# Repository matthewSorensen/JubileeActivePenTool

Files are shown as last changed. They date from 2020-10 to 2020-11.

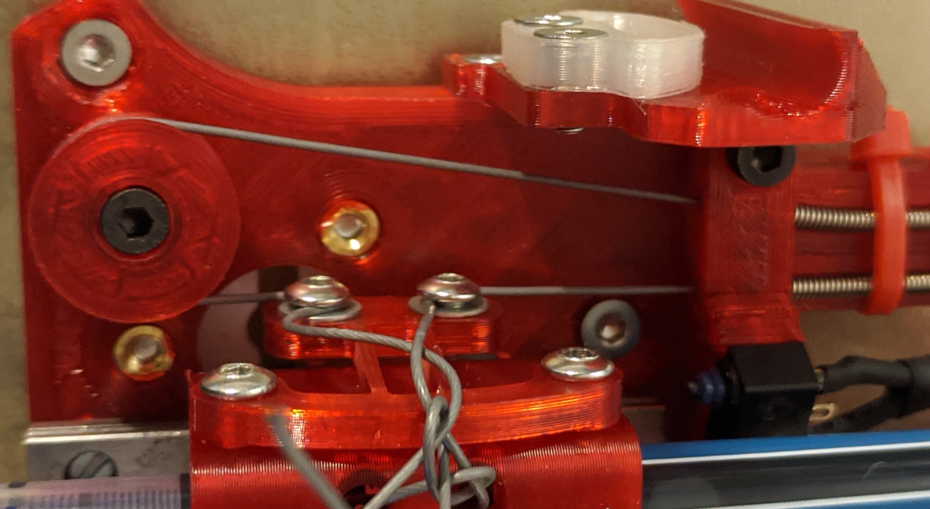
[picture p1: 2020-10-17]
photos/ToolCableRouting.jpg

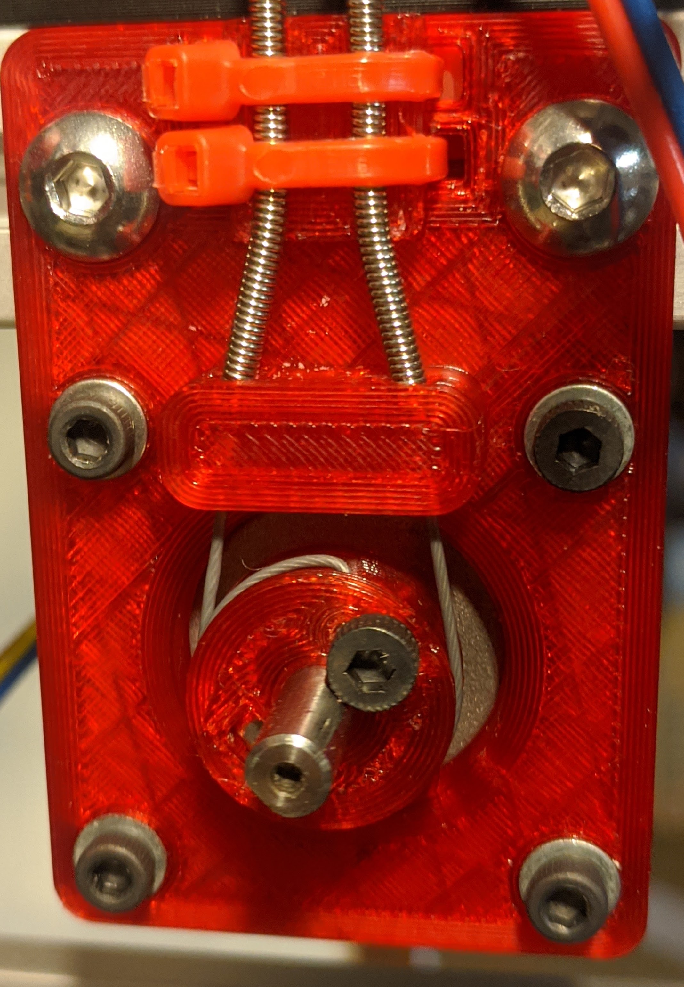
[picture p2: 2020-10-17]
photos/MotorPulley.jpg

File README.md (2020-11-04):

Jubilee Plotter Tool
======

An actively-driven pen plotter toolhead for the [Jubilee](https://jubilee3d.com/) project.

## Limitations!

My machine's "ooze control assembly" is placed significantly lower than on a standard Jubilee, so I have
enough room to mount the motor/pulley assembly on the top bar, directly under the tool dock. In that
configuration, a stock 600mm spring guide is comfortably long enough to cover the full build area. However,
on a stock machine that requires the motor/pulley assembly to be mounted on the lower extrusion, a
longer (650mm?) spring guide is probably a good idea.

At the moment, I'm using a silly large stepper motor - this design is probably compatible with
a smaller "pancake" style stepper, but that is untested at the moment.

## Printed Parts

Print one of each stl in the *meshes* folder in PLA using the [standard Jubilee settings](https://jubilee3d.com/index.php?title=3D_Printed_Parts)
and the provided orientation. Or not, you're a responsible adult and can choose part orientation and
printer settings.

## BOM

* 1x stock Jubilee 600mm spring guide kit, consisting of:

    * 1600mm length of Low-Stretch Coated Wire Rope Braided, 18-8 Stainless Steel, 7 x 19, 0.024" Diameter

    * 2x600mm lengths of SG-088-020-120 spring guide, 0.020" dia wire, 0.088" OD, Type 302 Stainless

* 55mm LWL7B miniature linear rail and carriage

* NEMA17 stepper motor

* 4x M3 brass heated insert nut, McMaster 94180A331 - same used for the rest of the Jubilee build.

* M3 square nut - same used for the rest of the Jubilee build

* 5x M3 Buttonhead Screw, 6mm long (Bolt Depot 7218)

* 5x M3 Buttonhead Screw, 8mm long (Bolt Depot 7219)

* 5x M3 Buttonhead Screw, 12mm long (Bolt Depot 7221)

* 6x M3 washers (Bolt Depot 4513)

* 2x M5 Buttonhead Screw, 10mm long (Bolt Depot 6632)

* 2x M5 drop-in nuts for 20x20 extrusion

* M3 setscrew, 5mm long (Bolt Depot 8706)

* 4x M2.5 screws or bolts, 8mm-10mm long - must have heads compatible with linear rail

* 4x M2 machine screw, 8mm long (Bolt Depot)

* 1x MR103-ZZ bearing (or any 3mm ID/10mm OD/4mm tall bearing)

* 1x standard Jubilee limit switch

* Two strand wire for limit switch

* Small zipties

* 1 set of standard Jubilee tool plate hardware - steel balls, insert nuts, screws, delrin wedge plate etc...

* 4x M3x8 flathead screws (Bolt Depot 7213)

* 4x 5x9x2 Buna-N O-rings (McMaster 9262K165)

## Instructions

Nope, not yet. Ask me on discord - maybe I'll take more photos of the pulley wire routing?

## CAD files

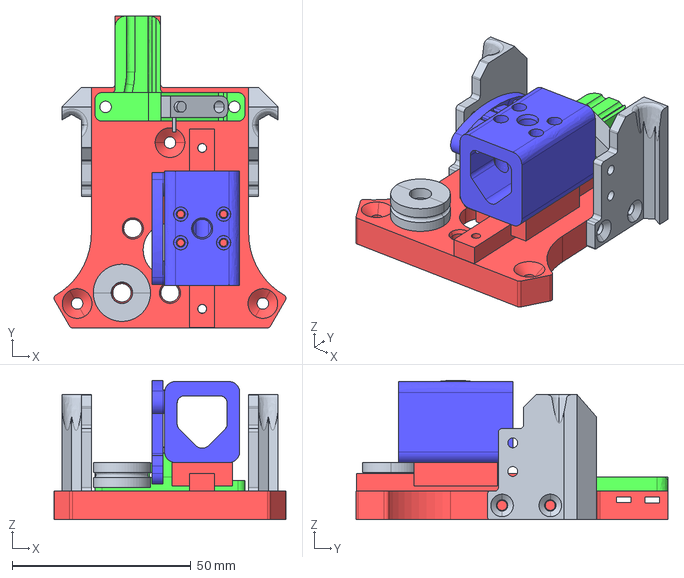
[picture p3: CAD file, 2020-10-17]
meshes/ToolAssembly.stp
64.9 x 87.2 x 39.0 mm

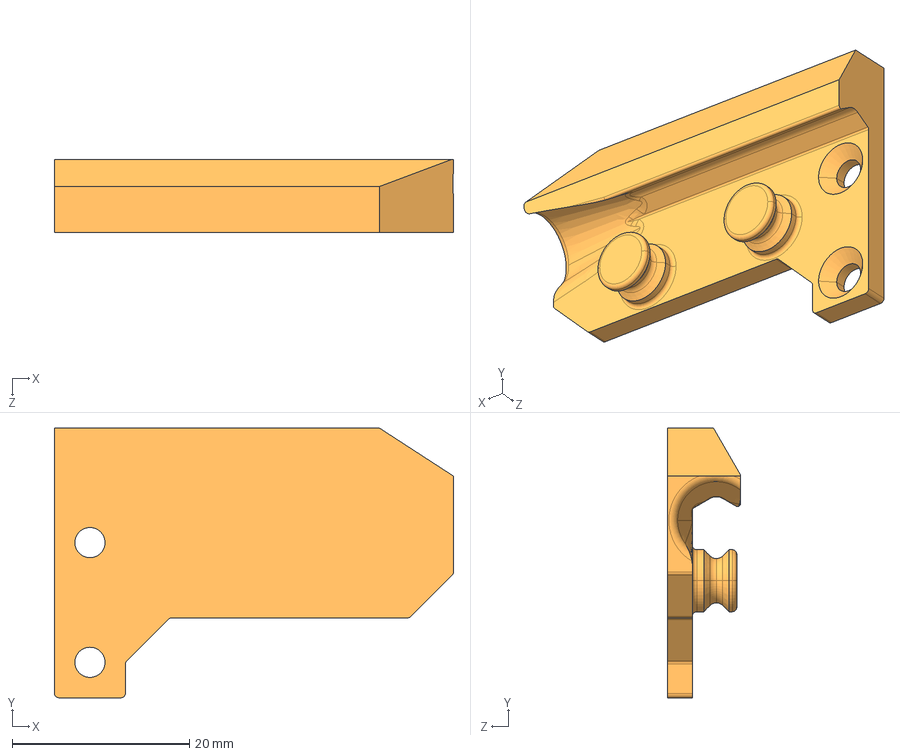
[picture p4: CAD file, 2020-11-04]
meshes/HalfWing.stp
45.0 x 30.4 x 8.20 mm

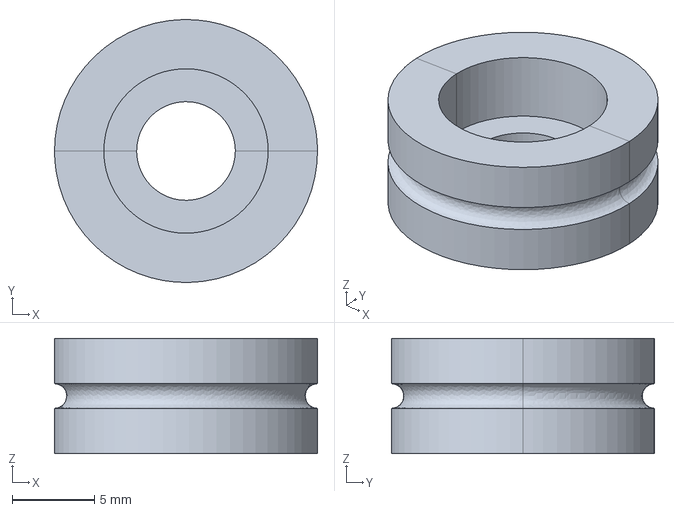
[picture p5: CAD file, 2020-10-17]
meshes/PassivePulley.stp
16.0 x 16.0 x 7.00 mm

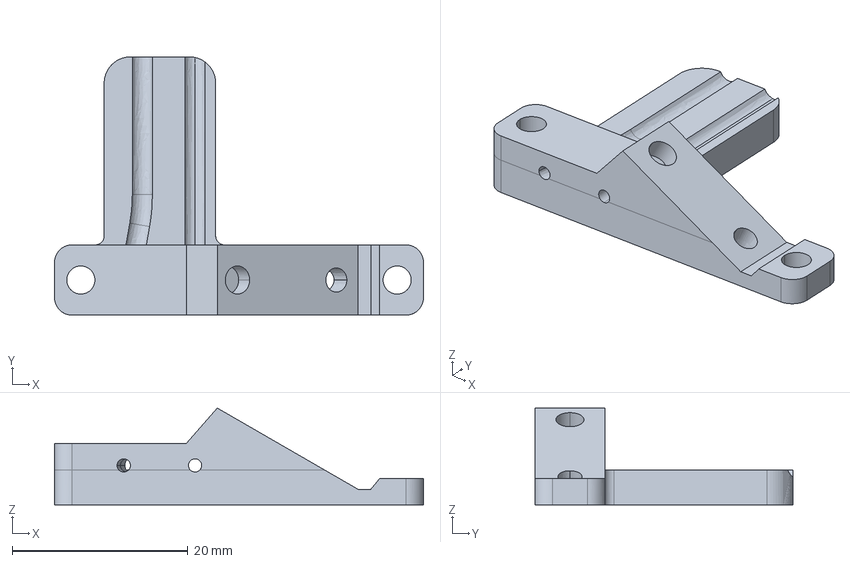
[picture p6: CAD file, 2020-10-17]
meshes/CableHolder.stp
42.0 x 29.4 x 11.0 mm

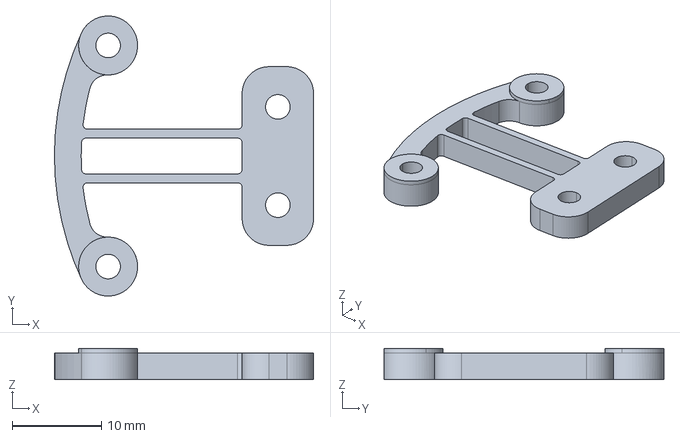
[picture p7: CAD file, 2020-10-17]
meshes/Flexure.stp
29.0 x 31.3 x 3.50 mm

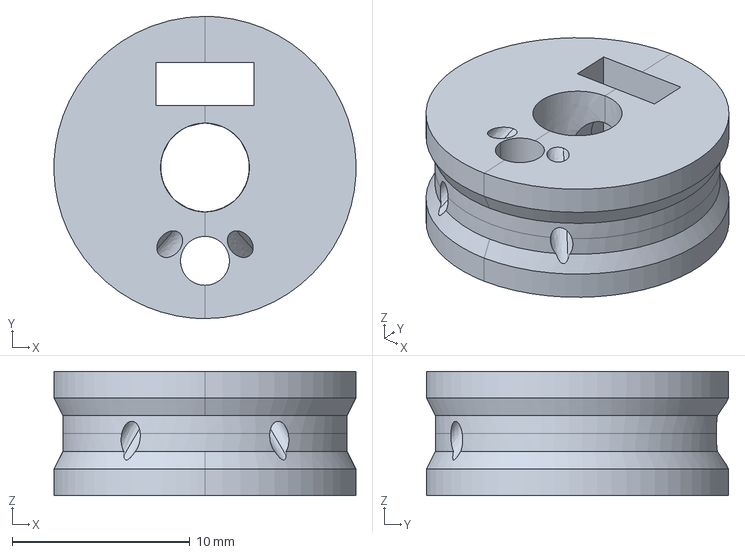
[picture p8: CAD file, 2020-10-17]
meshes/MotorPulley.stp
17.0 x 17.0 x 7.00 mm

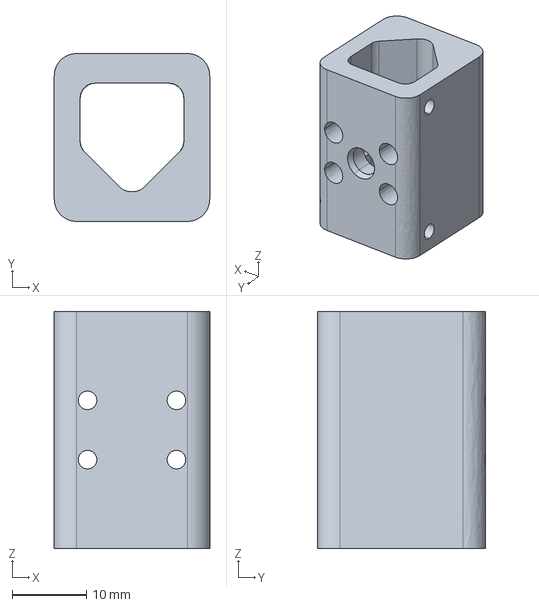
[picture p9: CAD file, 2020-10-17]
meshes/PenHolder.stp
21.0 x 22.7 x 32.0 mm

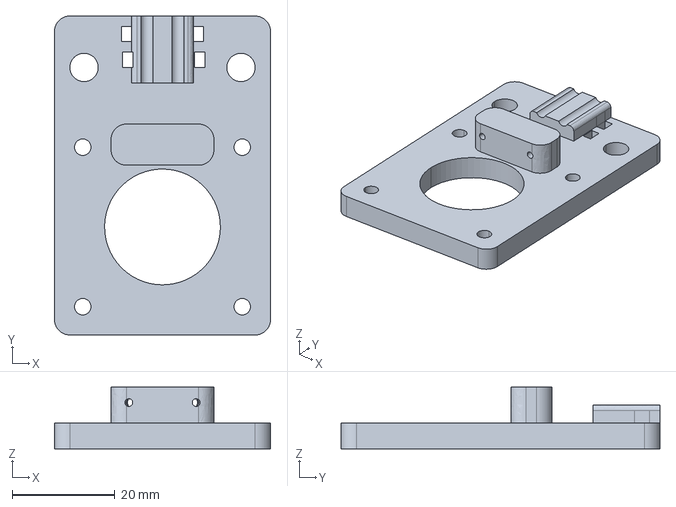
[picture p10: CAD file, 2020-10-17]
meshes/MotorMount.stp
42.0 x 62.0 x 12.0 mm

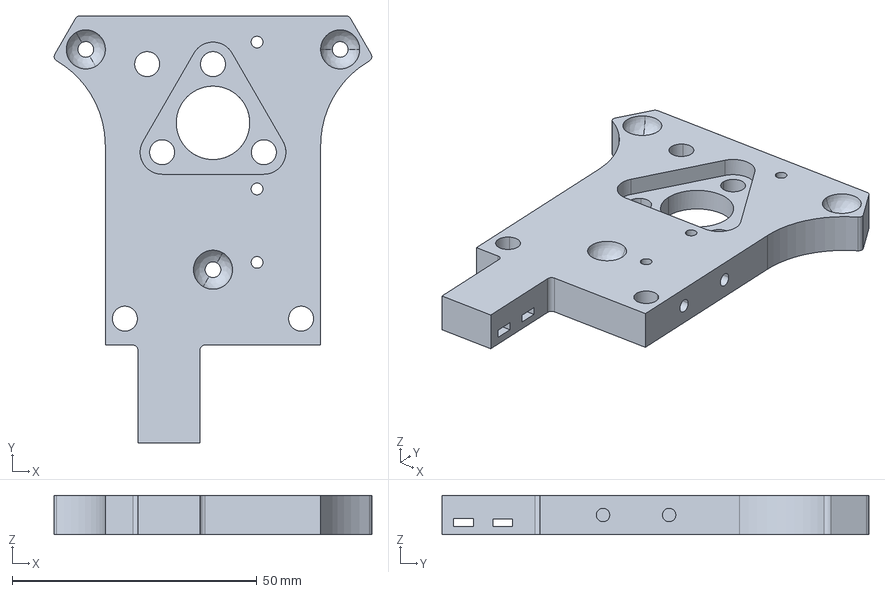
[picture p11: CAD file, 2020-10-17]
meshes/ToolPlate.stp
64.9 x 87.2 x 8.00 mm

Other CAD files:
meshes/CableHolder.stl
meshes/Flexure.stl
meshes/HalfWing.stl
meshes/MotorMount.stl
meshes/MotorPulley.stl
meshes/PassivePulley.stl
meshes/PenHolder.stl
meshes/ToolPlate.stl

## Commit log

2020-10-17 Here it is
    [CableHolder.stl, CableHolder.stp, Flexure.stl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]
2020-10-17 Oops I forgot 3 insert nuts
2020-11-04 New O-ring half-height wings, courtesty of Mr. Hobbit and Reefing Ninja
    [HalfWing.stl, HalfWing.stp]
